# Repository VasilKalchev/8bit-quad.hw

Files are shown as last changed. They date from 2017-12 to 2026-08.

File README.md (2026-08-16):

# 8bit-quad

Flight controller **PCB** for a custom-built quadcopter based on the ATmega328
microcontroller. An IMU, an nRF24L01+ radio and four ESC outputs on a 113 mm
octagon shaped to the top plate of an F450 frame.

It was etched at home, populated, flown, and retired. This repository is an
archive of it, not a design anyone is expected to build. [The firmware that
ran on it](https://github.com/VasilKalchev/8bit-quad) is in its own
repository.

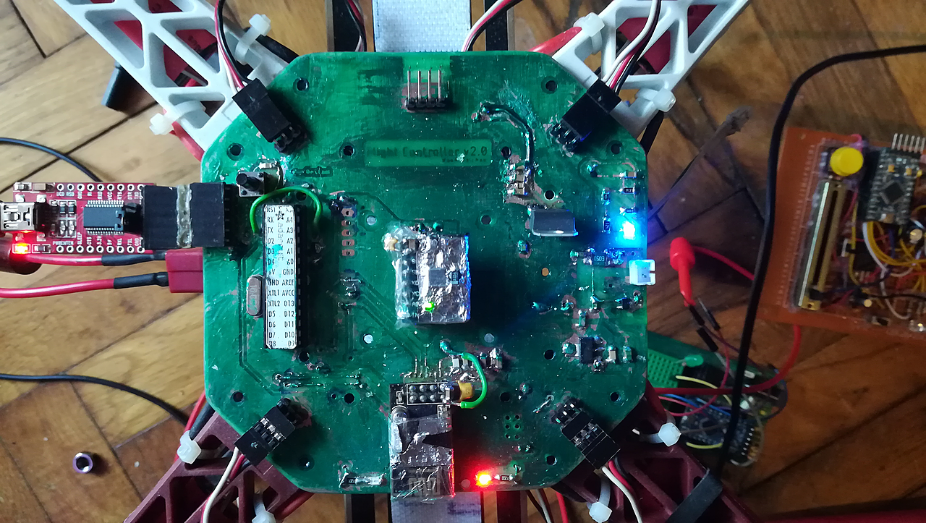
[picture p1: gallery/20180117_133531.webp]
the populated board


<sub>The board on the frame with an FTDI adapter attached. The remote is on
the right, on protoboard. It never had a PCB; what it had to provide is in
<a href="rc/">rc/</a>.</sub>

<table>
<tr>
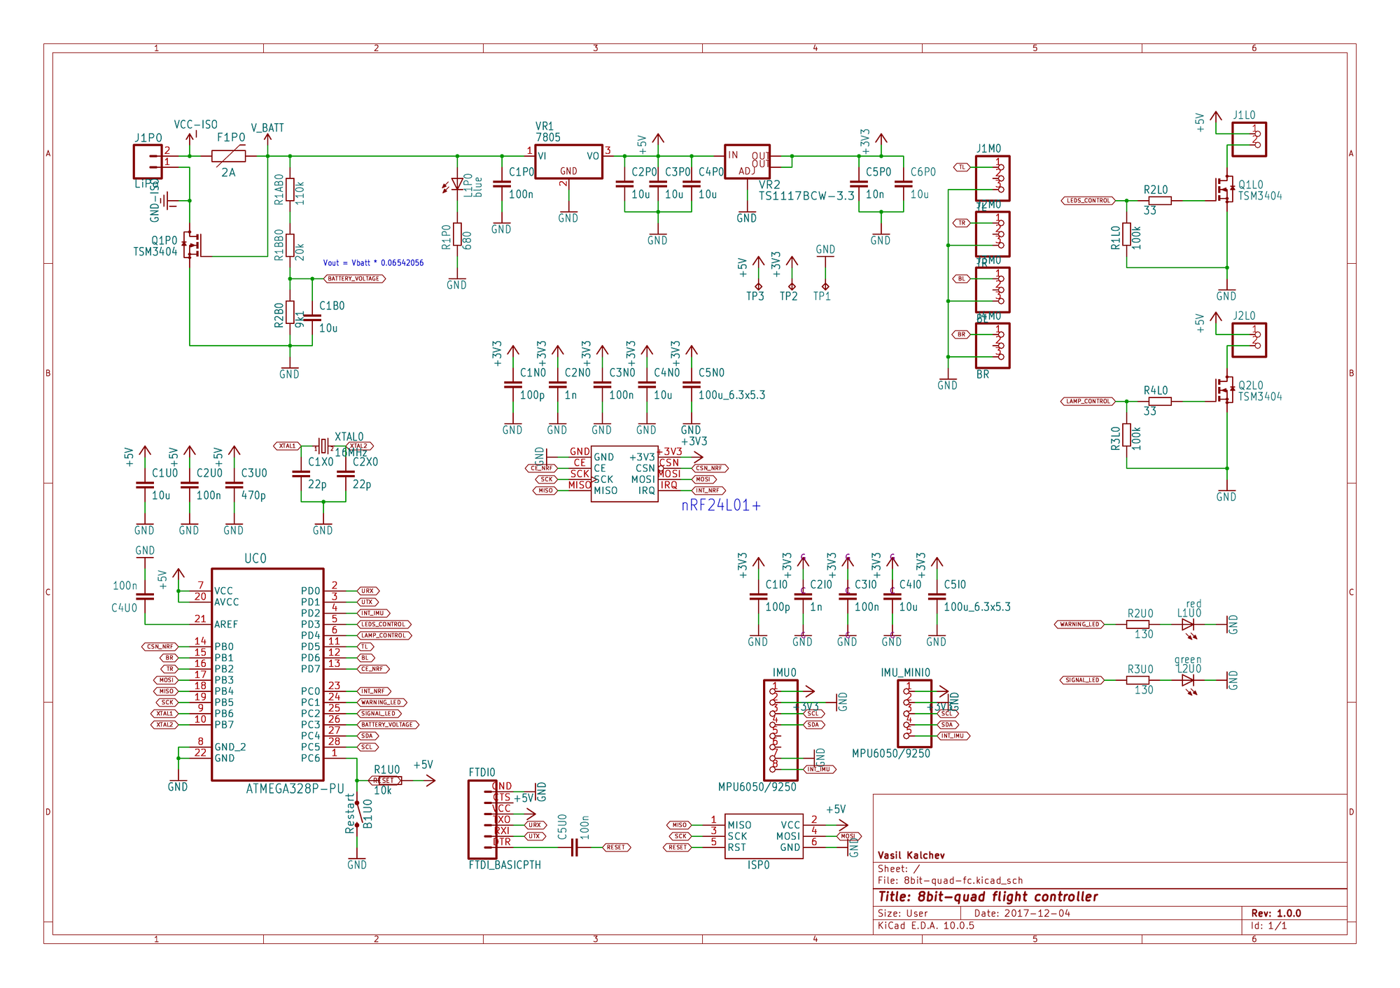
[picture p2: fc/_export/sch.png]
schematic
<td width="50%"></td>
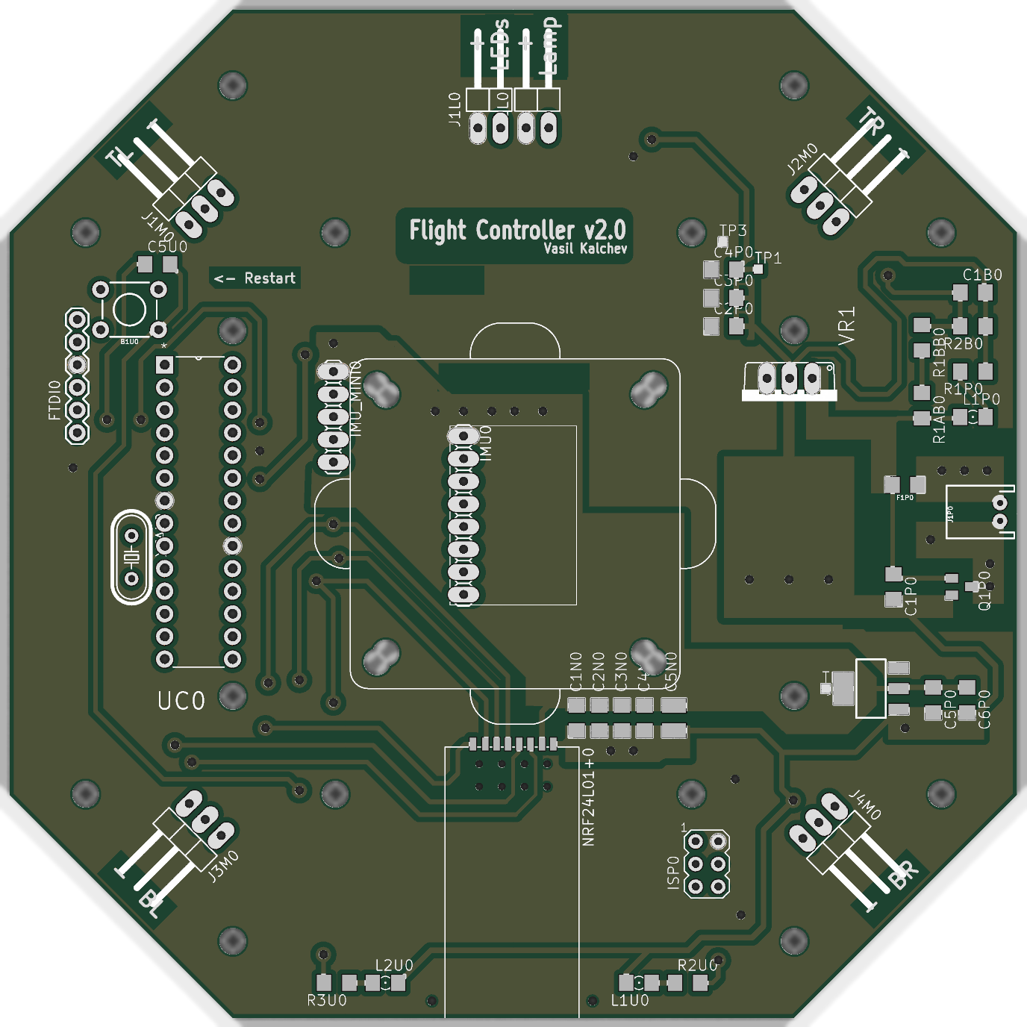
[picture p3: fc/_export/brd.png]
board
<td width="50%"></td>
</tr>
<tr>
<td align="center"><sub>schematic, click for the PDF</sub></td>
<td align="center"><sub>board</sub></td>
</tr>
</table>

```
fc/          KiCad 10 project, symbols and footprints included
  _export/   schematic and board images
  bom.txt    62 components
rc/          what the remote had to provide
gallery/     photographs
```

Everything the project needs is inside it. There are no dependencies on
installed libraries.

## The board

**The outline** is a 113 mm octagon because the board was originally meant to
*be* the F450's top plate rather than sit on it. A load-bearing flight
controller: the arms bolt through it, every landing is absorbed by the PCB,
the frame's vibration is piped straight into the IMU with nothing in between,
and any crash that would have cracked a plate worth a couple of euros instead
cracks the one part carrying all the electronics. Obvious in hindsight. Also
in foresight, to be fair.

The shape stayed regardless, and the board ended up bolted above the plate
like every other flight controller ever made.

Pin names below are the ones the firmware uses.

**The microcontroller** is an ATmega328P-PU in a DIP-28 socket with a 16 MHz
crystal, programmed over either an AVR ISP header or an FTDI header, with a
restart button next to it.

**The IMU** is an MPU6050 or MPU9250 breakout on I2C. There are two header
footprints for it, 1x8 and 1x5, so either of the two common module shapes
fits. Its interrupt lands on `PD2`. The outline drawn around it is an
anti-vibration plate, drawn when it was still meant to carry the IMU module
and nothing else. It ended up carrying the whole flight controller. So the
vibration problem was understood, and then solved by moving it one level up.

**The radio** is an nRF24L01+ PA/LNA module on hardware SPI, with `CE` on
`PD7`, `CSN` on `PB0` and the interrupt on `PC0`. The firmware's last revision
abandoned it for a PPM receiver, which takes over `PD2`.

**The ESC outputs** are four 3-pin headers labelled by frame position: `TL` on
`PD5`, `TR` on `PB2`, `BL` on `PD6`, `BR` on `PB1`. All four are hardware PWM
outputs, two on timer 0 and two on timer 1. Freeing timer 0 for that is why
the firmware ships its own Arduino core, which moves `millis()` onto timer 2.

**Power** arrived on a JST connector behind a 2 A PPTC and a MOSFET for
reverse polarity, then a 7805 and a TS1117 gave 5 V and 3.3 V. Battery voltage
reached `PC3` through 110k and 20k over 9k1, which the schematic notes as
`Vout = Vbatt * 0.06542056`.

**Indication** is a signal LED on `PC2` and a warning LED on `PC1`, plus two
low side MOSFETs switching an arm-LED header on `PD3` and a lamp header on
`PD4`.

Two measurements from a PicoScope in March 2022, on the built board: the ESC
drive edges rose in 11.2 ns at 5.065 V, and the IMU's I2C lines in 125 ns at
3.542 V.

## Etched at home

There are no gerbers and never were. The copper layers were printed onto
transparency and the board was etched by photoresist, so its rules are
generous: 18 mil clearance, 16 mil minimum track, 0.8 mm minimum drill. There
is [a video of the etching](https://youtu.be/nzKjSb2GAe4).

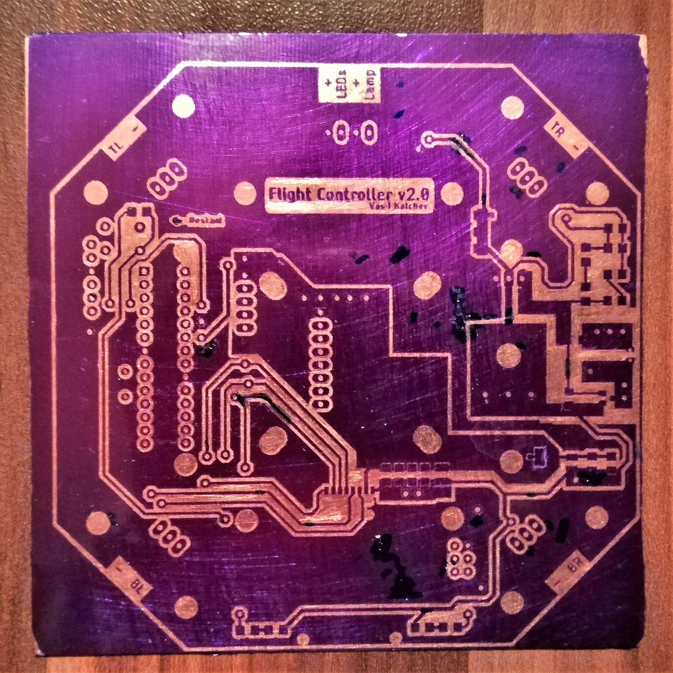
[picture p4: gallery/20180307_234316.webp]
the bare board


<sub>Etched, still purple from the photoresist, before drilling. The clearest
record of the artwork that exists.</sub>

> [!NOTE]
> DRC reports three errors, all on `J1P0`, the JST battery connector, whose
> pads and holes break the board's own rules. That is inherent to the
> footprint and predates the KiCad conversion; the board was built and flown
> that way. The rest is cosmetic silkscreen and thermal relief warnings.
> Connectivity is clean, with zero unconnected items once the zones are
> filled.

## History

This board is v2. The first flight controller was an Arduino Nano and an
nRF24L01+ hand wired on protoboard, and it is the reason this one is lettered
`Flight Controller v2.0`.

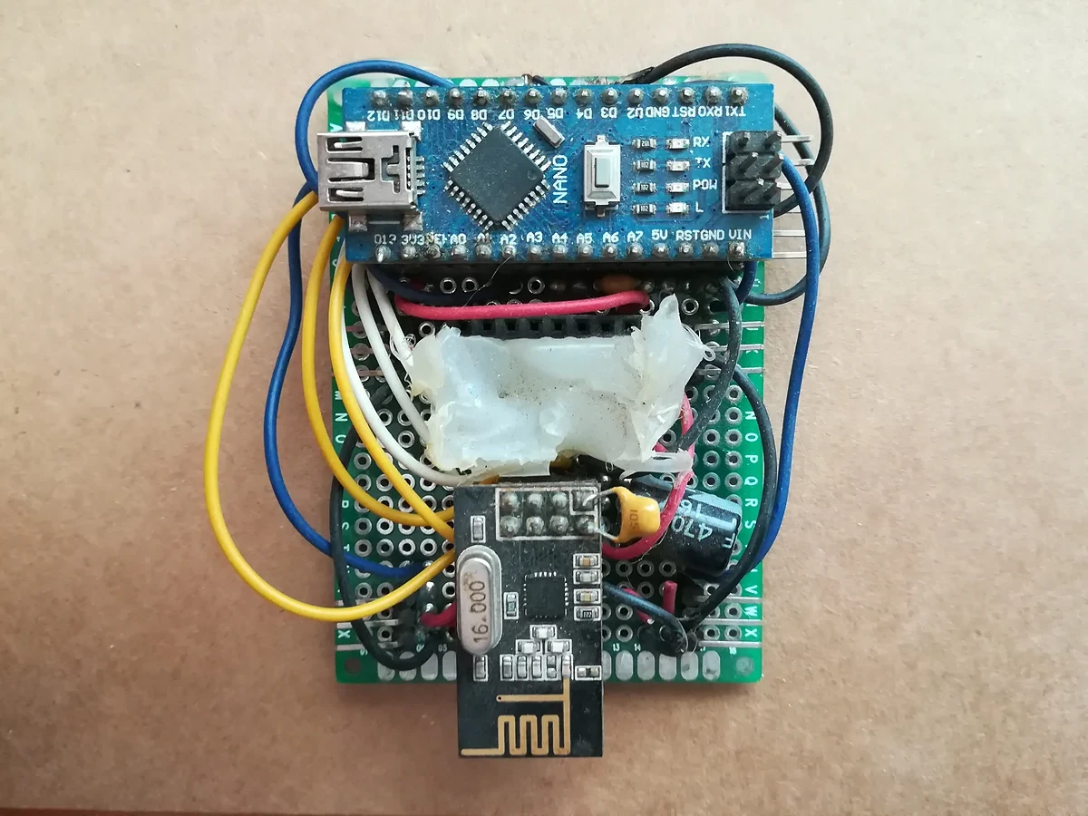
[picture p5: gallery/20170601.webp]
the first flight controller, on protoboard


<sub>v1, the protoboard flight controller this board replaced. Its IMU
module is missing here.</sub>

It was drawn in Eagle. Autodesk stopped developing standalone Eagle in 2024
and folded it into Fusion, so the design was converted to KiCad in 2026. The
original Eagle files are in the first commit of this repository and nowhere
else.

## Licence

Copyright Vasil Kalchev 2017

Licensed under CERN-OHL-P v2 or later. You may redistribute and modify this
source and make products using it under the terms of the
[CERN-OHL-P v2](https://ohwr.org/cern_ohl_p_v2.txt). This source is
distributed WITHOUT ANY EXPRESS OR IMPLIED WARRANTY, INCLUDING OF
MERCHANTABILITY, SATISFACTORY QUALITY AND FITNESS FOR A PARTICULAR PURPOSE.
Please see the CERN-OHL-P v2 for applicable conditions.

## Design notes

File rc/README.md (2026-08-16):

# Remote

There is no board design here. The remote was hand wired on protoboard around
an Arduino Nano and an nRF24L01+ module, and nothing was ever drawn for it. It
is visible on the right of
[`gallery/20180117_133531.webp`](../gallery/20180117_133531.webp).

What is recorded instead is what that hardware had to provide, read out of the
`8bit-quad-rc` firmware in the [firmware
repository](https://github.com/VasilKalchev/8bit-quad). The firmware is the
only surviving description of it, and it is identical in all three commits
that contain it, so there is one version of this to state.

## What it needs

An ATmega328P at 16 MHz with an nRF24L01+ on hardware SPI, three analog axes,
five digital inputs, an RGB LED and a warning LED. That is very nearly the
whole chip: only `PC4` and the crystal pins are left over.

| function | AVR | Arduino | direction | notes |
| --- | --- | --- | --- | ----- |
| throttle | `PC0` | A0 | analog in | not centred, full travel is the range |
| pitch | `PC1` | A1 | analog in | centre captured at boot |
| roll | `PC2` | A2 | analog in | centre captured at boot, doubles as yaw |
| flight mode | `PC3` | A3 | digital in | needs an external pull, 1 is ACRO |
| yaw mode | `PD2` | D2 | digital in | needs an external pull, 0 enables yaw |
| control mode | `PD4` | D4 | digital in | needs an external pull, 1 is MENU |
| function button | `PB2` | D10 | digital in | internal pull-up, 0 is active |
| stick button | `PC5` | A5 | digital in | internal pull-up |
| LED red | `PD3` | D3 | PWM out | `OC2B`, timer 2 |
| LED green | `PD5` | D5 | PWM out | `OC0B`, timer 0 |
| LED blue | `PD6` | D6 | PWM out | `OC0A`, timer 0 |
| LED warning | `PB1` | D9 | PWM out | `OC1A`, timer 1 |
| radio CE | `PD7` | D7 | out | nRF24L01+ |
| radio CSN | `PB0` | D8 | out | nRF24L01+ |
| SPI MOSI | `PB3` | D11 | out | nRF24L01+ |
| SPI MISO | `PB4` | D12 | in | nRF24L01+ |
| SPI SCK | `PB5` | D13 | out | nRF24L01+ |
| serial TX | `PD1` | D1 | out | 250000 baud |
| serial RX | `PD0` | D0 | in | serial command line |

## Things the pin list does not say

**There are three axes, not four.** Yaw has no stick of its own. Holding the
yaw mode input low turns the roll axis into yaw, negated, and scaled by 2.3 in
stabilize or 1.1 in acro.

**Pitch and roll centres are measured at power-on**, five averaged readings
each, so both sticks have to be at rest when the remote is switched on. There
is no stored calibration and no way to recentre without a reset. Throttle is
not centred at all.

**Three of the digital inputs have their internal pull-ups explicitly turned
off**: flight mode, yaw mode and control mode. Those three need pulls on the
board. The two buttons keep their internal pull-ups and are active low.

**The LEDs are active high**, driven low at startup, so common cathode. Red,
green and blue are one RGB LED that the firmware mixes into six colours; the
warning LED is separate.

**Timer 0 is not the Arduino timer.** The firmware moves `millis()` onto
timer 2 so that timer 0's two PWM outputs are free for the green and blue
channels. Timer 2 still drives red while keeping time, and timer 1 drives the
warning LED. This is the same swap the flight controller's Arduino core does,
and it is why the sketch targets `8bit-quad:avr:rc` rather than an Uno.

**The ADC** runs off AVCC with a prescaler of 32, ten bits.

**The radio** runs at 2 Mbps, maximum PA level, one retry with the longest
delay, over five pipe addresses based at `0x3A3A3A3A`.

**There is no battery sensing on the remote.** The battery voltage it displays
arrives from the drone by telemetry.

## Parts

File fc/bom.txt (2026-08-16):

Bill of materials, 8bit-quad flight controller

Generated from the KiCad schematic, so it is complete by construction.
Regenerate with:

  kicad-cli sch export bom --group-by 'Value,Footprint' \
      --fields 'Reference,Value,Footprint,${QUANTITY}' 8bit-quad-fc.kicad_sch

Values are as drawn, with Eagle package suffixes stripped where they only
repeated the package column. Symbol names come from the original Eagle
schematic.

Resistors
---------

  Qty  Value  Symbol  Package  References
    1  110k   R-EU    R1206    R1AB0
    1  20k    R-EU    R1206    R1BB0
    2  100k   R-EU    R1206    R1L0,R3L0
    1  680    R-EU    R1206    R1P0
    1  10k    R-EU    R1206    R1U0
    1  9k1    R-EU    R1206    R2B0
    2  33     R-EU    R1206    R2L0,R4L0
    2  130    R-EU    R1206    R2U0,R3U0

Capacitors
----------

  Qty  Value  Symbol  Package  References
    8  10u    C-EU    C1206    C1B0,C1U0,C2P0,C3P0,C4I0,C4N0,C4P0,C6P0
    2  100p   C-EU    C1206    C1I0,C1N0
    6  100n   C-EU    C1206    C1P0,C2U0,C3I0,C3N0,C4U0,C5U0
    2  22p    C-EU    C1206    C1X0,C2X0
    2  1n     C-EU    C1206    C2I0,C2N0
    1  470p   C-EU    C1206    C3U0
    2  100u   C-EU    C3225    C5I0,C5N0
    1  10n    C-EU    C1206    C5P0

Semiconductors
--------------

  Qty  Value          Symbol         Package            References
    1  blue           LED            1206               L1P0
    1  red            LED            1206               L1U0
    1  green          LED            1206               L2U0
    3  TSM3404        BSS123         SOT23              Q1L0,Q1P0,Q2L0
    1  ATMEGA328P-PU  ATMEGA328P-PU  DIP254P762X457-28  UC0
    1  7805           78             TO220V             VR1
    1  TS1117BCW-3.3  V_REG_LM1117   SOT223             VR2

Crystal and fuse
----------------

  Qty  Value  Symbol   Package  References
    1  2A     PPTC     1206     F1P0
    1  16MHz  CRYSTAL  HC49_S   XTAL0

Modules
-------

  Qty  Value         Symbol                         Package               References
    1  MPU6050/9250  PINHD-1X8                      1X08                  IMU0
    1  MPU6050/9250  PINHD-1X5                      1X05                  IMU_MINI0
    1  nRF24L01+     NRF24L01+_PA_LNA_BREAKOUT_SMD  NRF24L01+_PA_LNA_SMD  NRF24L01+0

Connectors and headers
----------------------

  Qty  Value            Symbol      Package     References
    1  FTDI Basic       FTDI_BASIC  FTDI_BASIC  FTDI0
    1  AVRISP-6         AVRISP      AVRISP      ISP0
    2  1x2 right angle  PINHD-1X2   1X02_90     J1L0,J2L0
    1  TL               PINHD-1X3   1X03_90     J1M0
    1  LiPo             CONN_02     JST-2-PTH   J1P0
    1  TR               PINHD-1X3   1X03_90     J2M0
    1  BL               PINHD-1X3   1X03_90     J3M0
    1  BR               PINHD-1X3   1X03_90     J4M0

Switch and test points
----------------------

  Qty  Value    Symbol                 Package                   References
    1  Restart  MOMENTARY-SWITCH-SPST  TACTILE_SWITCH_PTH_6.0MM  B1U0
    1  0V       TP                     TP10SQ                    TP1
    1  3.3V     TP                     TP10SQ                    TP2
    1  5.0V     TP                     TP10SQ                    TP3

Total: 62 components in 40 distinct lines.

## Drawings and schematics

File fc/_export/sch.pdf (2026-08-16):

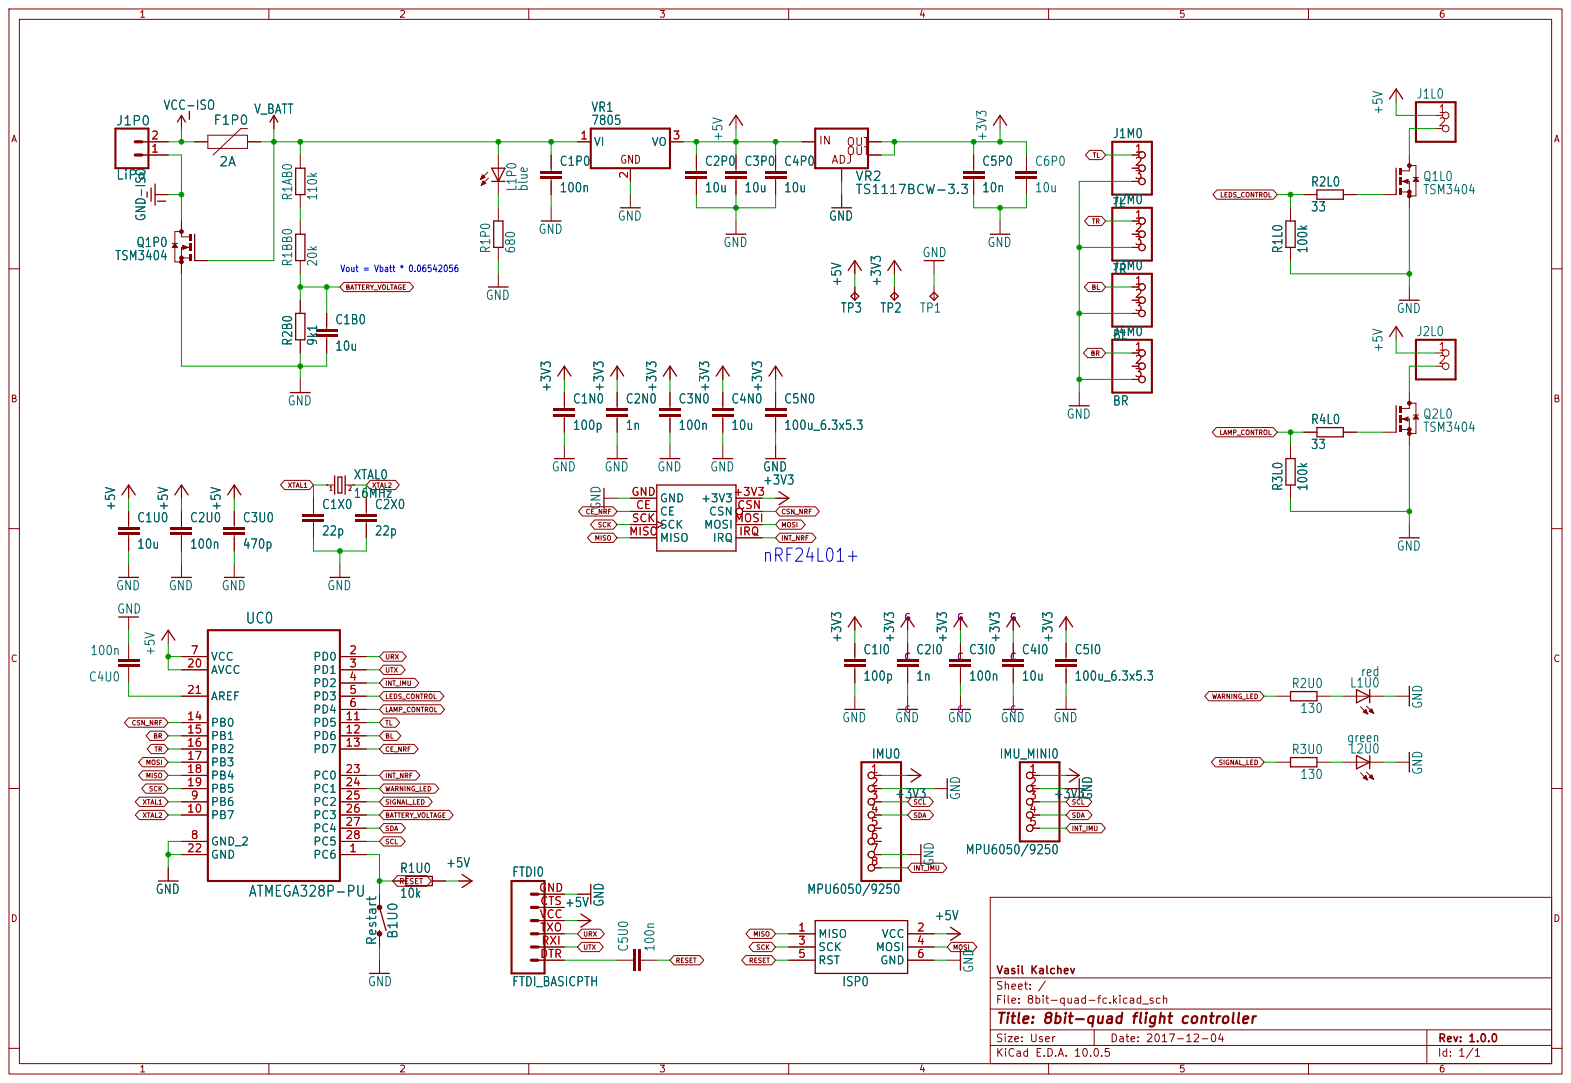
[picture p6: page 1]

Sheet: /
File: 8bit-quad-fc.kicad_sch
Title: 8bit-quad flight controller

Size: User | Rev: 1.0.0
KiCad E.D.A. 10.0.5 | Id: 1/1

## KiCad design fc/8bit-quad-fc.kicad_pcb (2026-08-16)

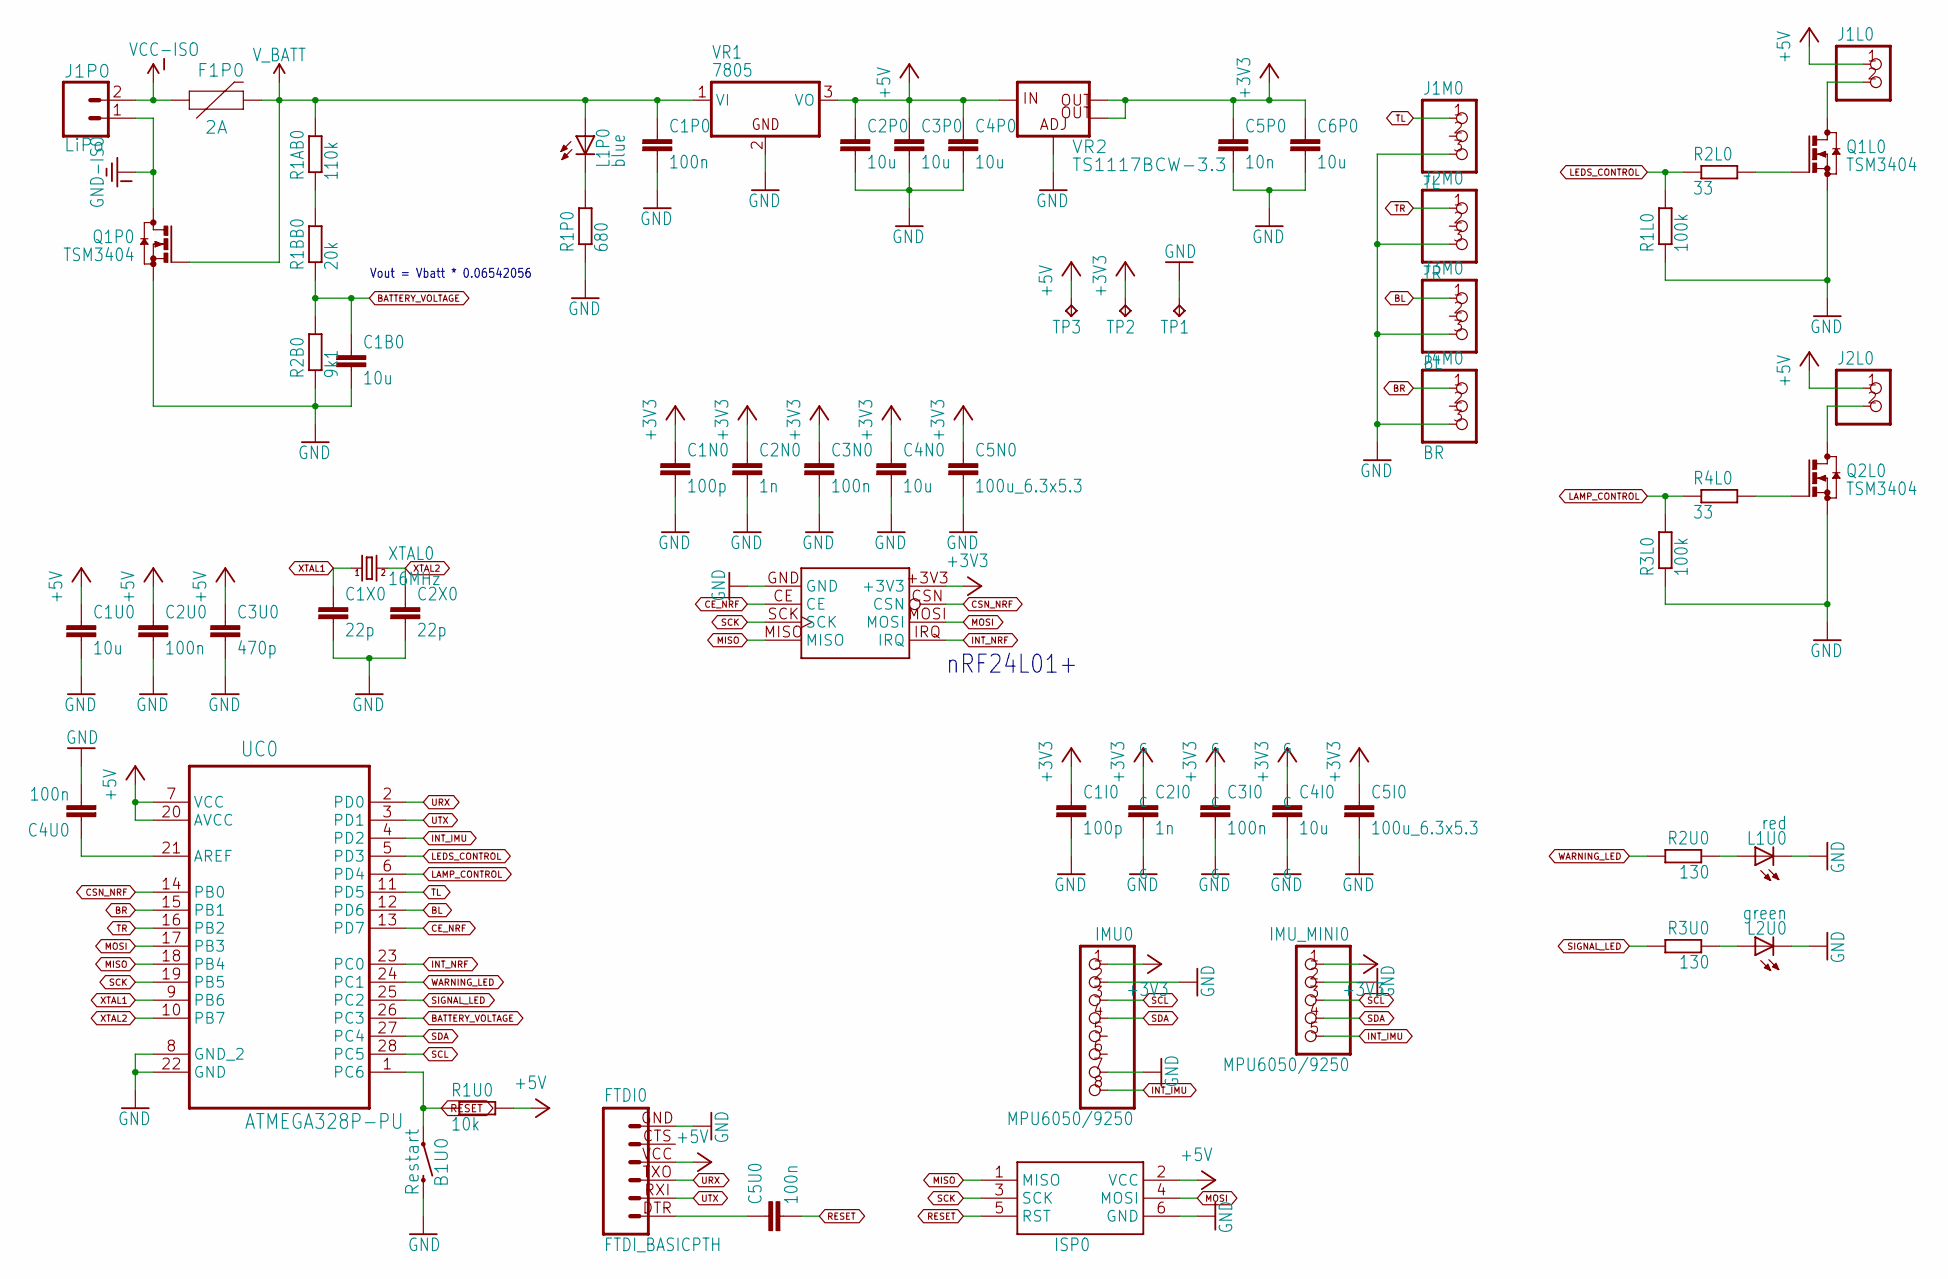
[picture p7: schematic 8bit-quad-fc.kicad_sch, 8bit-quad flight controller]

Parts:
B1U0: Restart; TACTILE_SWITCH_PTH_6.0MM
C1B0, C1U0, C2P0, C3P0, C4I0, C4N0, C4P0, C6P0: 10u; C1206
C1I0, C1N0: 100p; C1206
C1P0, C2U0, C3I0, C3N0, C4U0, C5U0: 100n; C1206
C1X0, C2X0: 22p; C1206
C2I0, C2N0: 1n; C1206
C3U0: 470p; C1206
C5I0, C5N0: 100u_6.3x5.3; C3225
C5P0: 10n; C1206
F1P0: 2A; 1206
FTDI0: FTDI_BASICPTH; FTDI_BASIC
IMU0: MPU6050/9250; 1X08
IMU_MINI0: MPU6050/9250; 1X05
ISP0: AVRISP-6; AVRISP
J1L0, J2L0: PINHD-1X2/90; 1X02_90
J1M0: TL; 1X03_90
J1P0: LiPo; JST-2-PTH
J2M0: TR; 1X03_90
J3M0: BL; 1X03_90
J4M0: BR; 1X03_90
L1P0: blue; 1206
L1U0: red; 1206
L2U0: green; 1206
NRF24L01+0: nRF24L01+; NRF24L01+_PA_LNA_SMD
Q1L0, Q1P0, Q2L0: TSM3404; SOT23
R1AB0: 110k; R1206
R1BB0: 20k; R1206
R1L0, R3L0: 100k; R1206
R1P0: 680; R1206
R1U0: 10k; R1206
R2B0: 9k1; R1206
R2L0, R4L0: 33; R1206
R2U0, R3U0: 130; R1206
TP1: 0V; TP10SQ
TP2: 3.3V; TP10SQ
TP3: 5.0V; TP10SQ
UC0: ATMEGA328P-PU; DIP254P762X457-28; MPN ATMEGA328P-PU
VR1: 7805; TO220V
VR2: TS1117BCW-3.3; SOT223
XTAL0: 16MHz; HC49_S

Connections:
+3V3: C1I0.1, C1N0.1, C2I0.1, C2N0.1, C3I0.1, C3N0.1, C4I0.1, C4N0.1, C5I0.1, C5N0.1, C5P0.1, C6P0.1, IMU0.1, IMU_MINI0.1, NRF24L01+0.+3V3, TP2.TP, VR2.2 (OUT), VR2.4 (OUT)
+5V: C1U0.1, C2P0.1, C2U0.1, C3P0.1, C3U0.1, C4P0.1, FTDI0.VCC (4), ISP0.2 (VCC), J1L0.1, J2L0.1, R1U0.2, TP3.TP, UC0.7 (VCC), UC0.20 (AVCC), VR1.3 (VO), VR2.3 (IN)
BATTERY_VOLTAGE: C1B0.1, R1BB0.1, R2B0.2, UC0.26 (PC3)
BL: J3M0.1, UC0.12 (PD6)
BR: J4M0.1, UC0.15 (PB1)
CE_NRF: NRF24L01+0.CE, UC0.13 (PD7)
CSN_NRF: NRF24L01+0.CSN, UC0.14 (PB0)
GND: B1U0.3 (2), C1B0.2, C1I0.2, C1N0.2, C1P0.2, C1U0.2, C1X0.2, C2I0.2, C2N0.2, C2P0.2, C2U0.2, C2X0.2, C3I0.2, C3N0.2, C3P0.2, C3U0.2, C4I0.2, C4N0.2, C4P0.2, C4U0.2, C5I0.2, C5N0.2, C5P0.2, C6P0.2, FTDI0.GND (6), IMU0.2, IMU0.7, IMU_MINI0.2, ISP0.6 (GND), J1M0.3, J2M0.3, J3M0.3, J4M0.3, L1U0.C, L2U0.C, NRF24L01+0.GND, Q1L0.2 (S), Q1P0.2 (S), Q2L0.2 (S), R1L0.1, R1P0.1, R2B0.1, R3L0.1, TP1.TP, UC0.8 (GND_2), UC0.22 (GND), VR1.2 (GND), VR2.1 (ADJ)
GND-ISO: J1P0.1, Q1P0.3 (D)
INT_IMU: IMU0.8, IMU_MINI0.5, UC0.4 (PD2)
INT_NRF: NRF24L01+0.IRQ, UC0.23 (PC0)
LAMP_CONTROL: R3L0.2, R4L0.1, UC0.6 (PD4)
LAMP_SINK: J2L0.2, Q2L0.3 (D)
LEDS_CONTROL: R1L0.2, R2L0.1, UC0.5 (PD3)
LEDS_SINK: J1L0.2, Q1L0.3 (D)
MISO: ISP0.1 (MISO), NRF24L01+0.MISO, UC0.18 (PB4)
MOSI: ISP0.4 (MOSI), NRF24L01+0.MOSI, UC0.17 (PB3)
unnamed: L2U0.A, R3U0.1
unnamed: R1AB0.1, R1BB0.2
unnamed: L1U0.A, R2U0.1
unnamed: Q1L0.1 (G), R2L0.2
unnamed: Q2L0.1 (G), R4L0.2
unnamed: L1P0.C, R1P0.2
unnamed: C4U0.1, UC0.21 (AREF)
unnamed: C5U0.1, FTDI0.DTR (1)
RESET: B1U0.1, C5U0.2, ISP0.5 (RST), R1U0.1, UC0.1 (PC6)
SCK: ISP0.3 (SCK), NRF24L01+0.SCK, UC0.19 (PB5)
SCL: IMU0.3, IMU_MINI0.3, UC0.28 (PC5)
SDA: IMU0.4, IMU_MINI0.4, UC0.27 (PC4)
SIGNAL_LED: R3U0.2, UC0.25 (PC2)
TL: J1M0.1, UC0.11 (PD5)
TR: J2M0.1, UC0.16 (PB2)
URX: FTDI0.TXO (3), UC0.2 (PD0)
UTX: FTDI0.RXI (2), UC0.3 (PD1)
VCC-ISO: F1P0.1, J1P0.2
V_BATT: C1P0.1, F1P0.2, L1P0.A, Q1P0.1 (G), R1AB0.2, VR1.1 (VI)
WARNING_LED: R2U0.2, UC0.24 (PC1)
XTAL1: C1X0.1, UC0.9 (PB6), XTAL0.1
XTAL2: C2X0.1, UC0.10 (PB7), XTAL0.2

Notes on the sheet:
Vout = Vbatt * 0.06542056
nRF24L01+

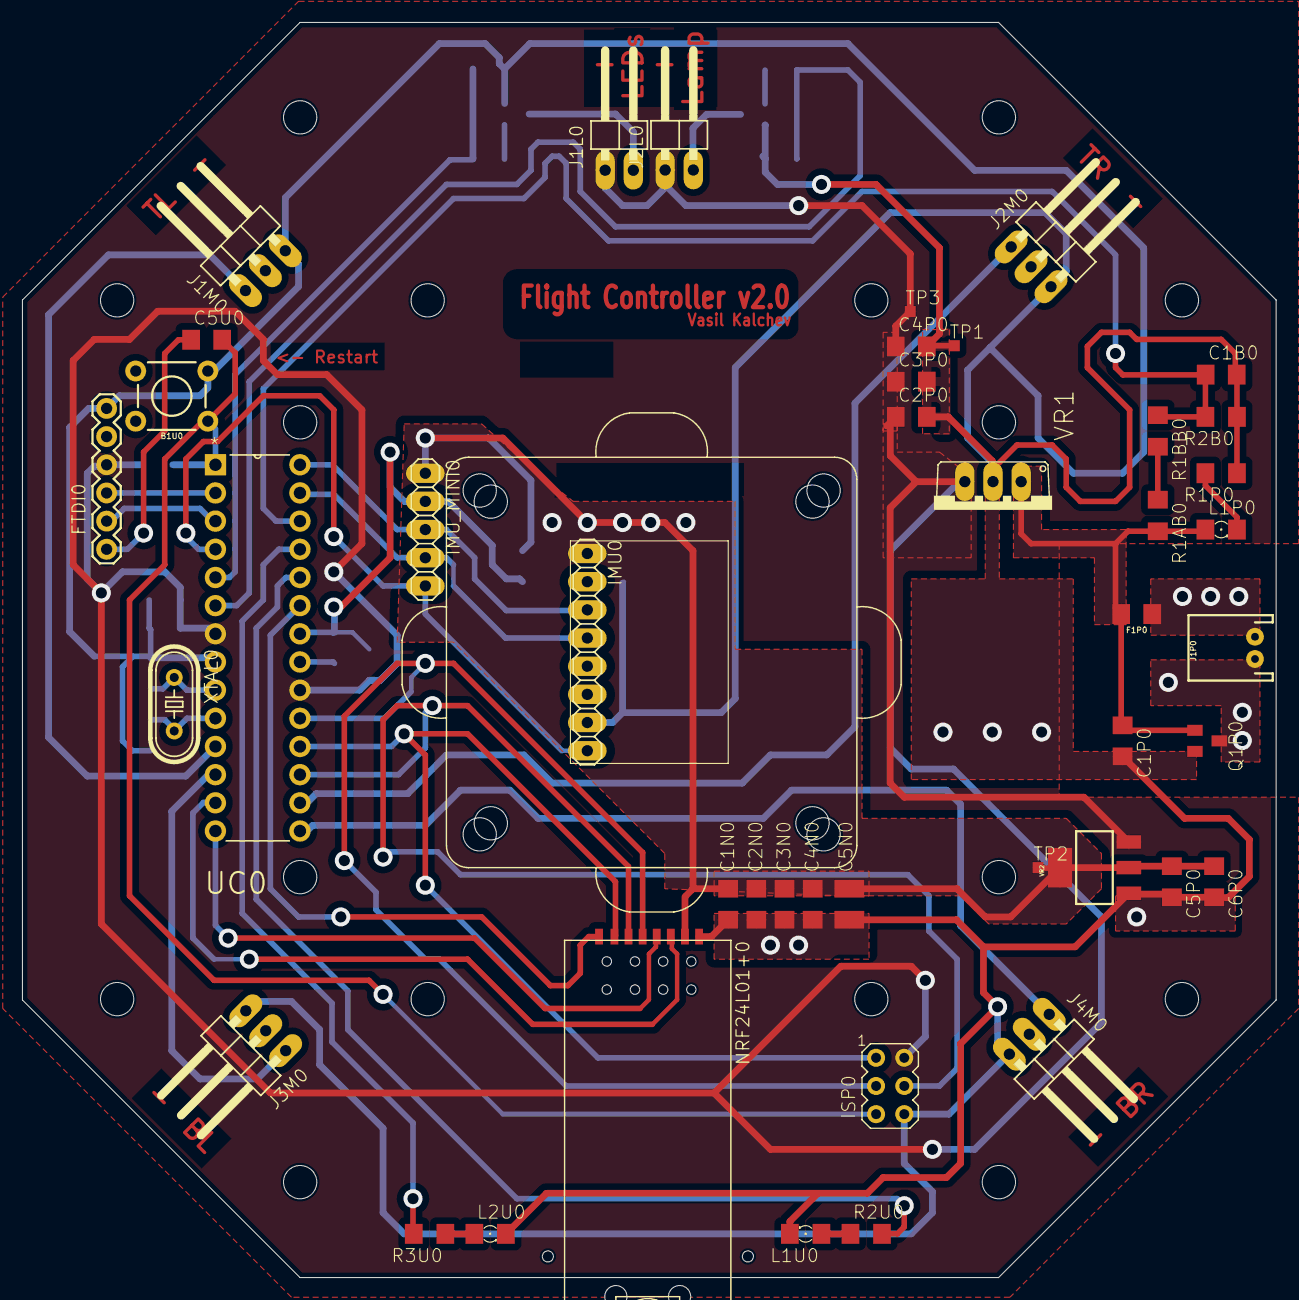
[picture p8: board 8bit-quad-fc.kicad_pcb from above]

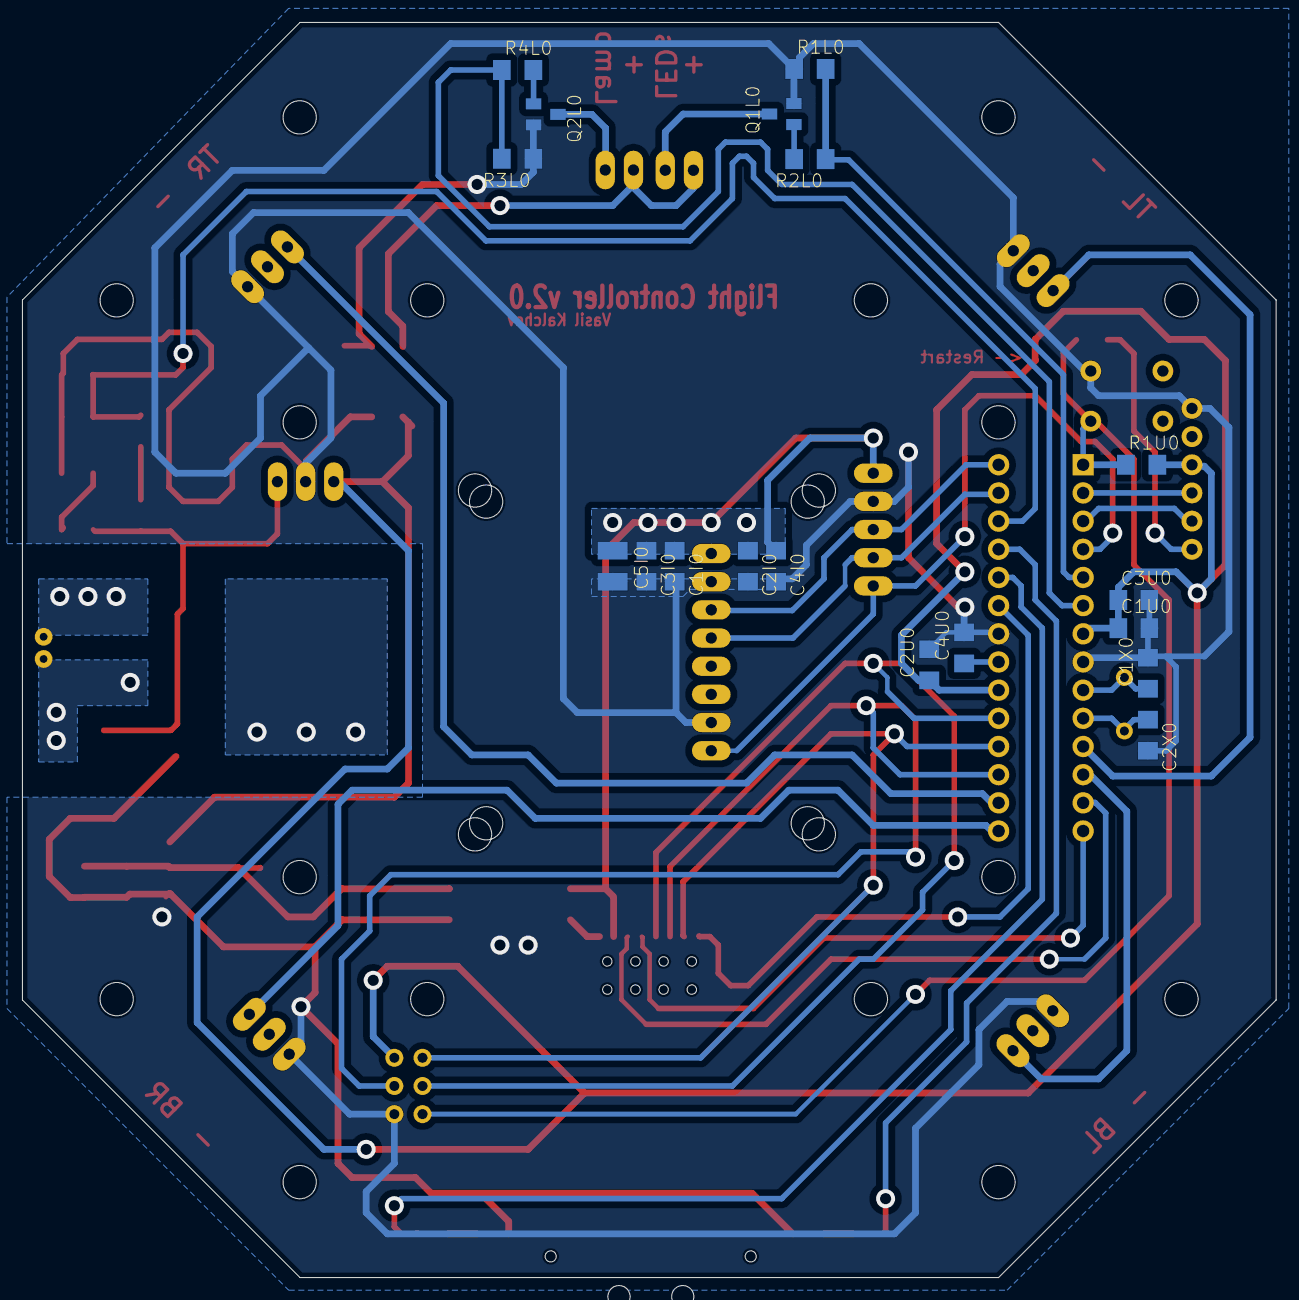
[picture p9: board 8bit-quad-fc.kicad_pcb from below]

Board: 2 copper layers, 113.0 x 113.2 mm, 66 parts (18 on the bottom side), 39 nets.

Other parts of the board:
H1, H2: 1 mm hole; HOLE_1MM
U$2: F450_TOP_PLATE
U$3: ANTI-VIBRATION_PLATE

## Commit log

2017-12-04 Flight controller board, drawn in Eagle and etched at home
    Two layer, 113 mm octagon cut to sit on the top plate of an F450 frame.
    ATmega328P at 16 MHz with an nRF24L01+ PA/LNA module, an MPU6050 or MPU9250
    on either an 8 pin or a 5 pin header, and four 3 pin ESC outputs labelled by
    frame position.
    Power comes in on a JST connector behind a 2 A PPTC and a MOSFET for reverse
    polarity, then a 7805 and a TS1117 for 5 V and 3.3 V. Battery voltage reaches
    the ADC through 110k and 20k over 9k1, which the schematic notes as
    Vout = Vbatt * 0.06542056. Two low side MOSFETs switch the LED and lamp
    headers, and there are FTDI and AVR ISP headers, a restart button, three
    indicator LEDs and three test p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
    [8bit-quad-fc.brd, 8bit-quad-fc.sch]
2018-03-07 Photographs of the etched board
    20180117_133531 is the populated board on the frame, powered, with an FTDI
    adapter attached and the nRF24 and IMU modules seated.
    20180307_234316 is a bare board straight on, still purple from the
    photoresist, before drilling and populating. It is the clearest surviving
    record of the artwork: the octagon, the TL, TR, BL and BR motor labels, the
    Restart, LEDs and Lamp legends, and the title block reading Flight Controller
    v2.0 with Vasil Kalchev under it. The 2026 lettering correction was measured
    from this photograph.
    The bare board is dated seven weeks after the populated one, which suggests a
    second board was etched. Not remembered either way, and nothing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
